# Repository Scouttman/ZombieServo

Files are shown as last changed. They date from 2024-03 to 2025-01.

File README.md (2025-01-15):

# ZombieServo
Motor Driver for some [aliexpress](https://www.aliexpress.com/item/1005004112490054.html) robotic serovos powered by simpleFOC and a STSPIN32g4
Runs simpleFOC forum post [here](https://community.simplefoc.com/t/zombie-servo-budget-high-torque-servo/4001)  
May also port the mit mini cheeta code to it if the torque control is good   
Position can be set with T i.e. set T6.28 will do one rotation (not sure why it is not a full rotation)  
The M command for simple foc is added but not tested  
20231021_143033 (1)
20231021_140654 (1)

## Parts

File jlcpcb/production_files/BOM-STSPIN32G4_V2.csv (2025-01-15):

Comment | Designator | Footprint | LCSC
Conn_01x03_MountingPin | J8 | JST_SH_BM03B-SRSS-TB_1x03-1MP_P1.00mm_Vertical | C145955
Conn_01x06_MountingPin | J9 | JST_SH_BM06B-SRSS-TB_1x06-1MP_P1.00mm_Vertical | C145958
20p | C18,C4 | C_0402_1005Metric | C1554
Q_Dual_NMOS_G1 | Q1,Q2,Q7 | V-DFN3030-8 (Type K) | C155503
33nf | C19 | C_0402_1005Metric | C1585
10uf 25v | C1,C6 | C_0805_2012Metric | C15850
USB_C_Receptacle_USB2.0 | J14 | USB_C_Receptacle_XKB_U262-16XN-4BVC11 | C165948
SS210 | D5 | D_SOD-323 | C191023
1N4148WS | D1,D10,D11,D12,D2,D7 | D_SOD-323 | C2128
LED | D3,D4_white2 | LED_0805_2012Metric | C2297
5.1k | R20 | R_0402_1005Metric | C23186
120 | R98 | R_0402_1005Metric | C25079
220 | R5,R6,R8 | R_0402_1005Metric | C25091
33 | R1,R13,R17,R18,R25,R4 | R_0402_1005Metric | C25105
10k | R11,R2,R3,R99 | R_0402_1005Metric | C25744
22k | R26,R27,R41,R47 | R_0402_1005Metric | C25768
1.5k | R23,R24,R44,R50 | R_0402_1005Metric | C25867
5.1k | R19 | R_0402_1005Metric | C25905
PRTR5V0U2X | D13 | SOT-143 | C2827688
1uF | C16,C24,C27 | C_0805_2012Metric | C28323
STSPIN32G4 | IC1 | STSPIN32G4 | C2858620
Conn_01x06_MountingPin | J6 | PinHeader_1x06_P1.27mm_Vertical | C2904934
Conn_01x12_MountingPin | J2 | 0.5K-A-12PBF | C2914207
BAT30k | D8 | D_SOD-523 | C2926449
100nF | C11,C41,C7,C9 | C_0402_1005Metric | C307331
18uh | L2 | L_1812_4532Metric | C394124
11k | R29,R53 | R_0402_1005Metric | C409665
1uF | C10,C8 | C_0402_1005Metric | C52923
220nF | C2 | C_0805_2012Metric | C5378
2.2uf | C21,C23,C26,C3 | C_1206_3216Metric | C650969
7mΩ | R15,R7 | R_1206_3216Metric | C76302
LED | D4_white1 | LED_0805_2012Metric | C84256
24mhz | Y3 | Crystal_SMD_3225-4Pin_3.2x2.5mm | C9002
TJA1057T/1Z | U2 | SOIC-8_3.9x4.9mm_P1.27mm | C961484
Conn_01x02_Female | J4 | PinHeader_1x02_P2.54mm_Vertical
Jumper_2_Bridged | JP8 | SolderJumper-2_P1.3mm_Bridged_RoundedPad1.0x1.5mm
NetTie_2 | NT1 | NetTie-2_SMD_Pad0.5mm
72.3k | R37 | R_0402_1005Metric
3.01k | R39 | R_0402_1005Metric
Jumper_2_Bridged | JP4 | SolderJumper-2_P1.3mm_Bridged_RoundedPad1.0x1.5mm
Jumper_2_Open | JP3 | SolderJumper-2_P1.3mm_Open_TrianglePad1.0x1.5mm
NetTie_2 | NT2 | NetTie-2_SMD_Pad0.5mm
MountingHole | H3 | MountingHole_2.2mm_M2
MountingHole | H2 | MountingHole_2.2mm_M2
MountingHole | H1 | MountingHole_2.2mm_M2
MountingHole | H4 | MountingHole_2.2mm_M2
Conn_01x03_Pin | J1 | JST_XH_B3B-XH-AM_1x03_P2.50mm_Vertical
Conn_01x03_MountingPin | J5 | JST_SH_BM03B-SRSS-TB_1x03-1MP_P1.00mm_Vertical
SW_Push | SW1 | SolderJumper-2_P1.3mm_Open_RoundedPad1.0x1.5mm
Jumper_2_Bridged | JP1 | SolderJumper-2_P1.3mm_Bridged_RoundedPad1.0x1.5mm

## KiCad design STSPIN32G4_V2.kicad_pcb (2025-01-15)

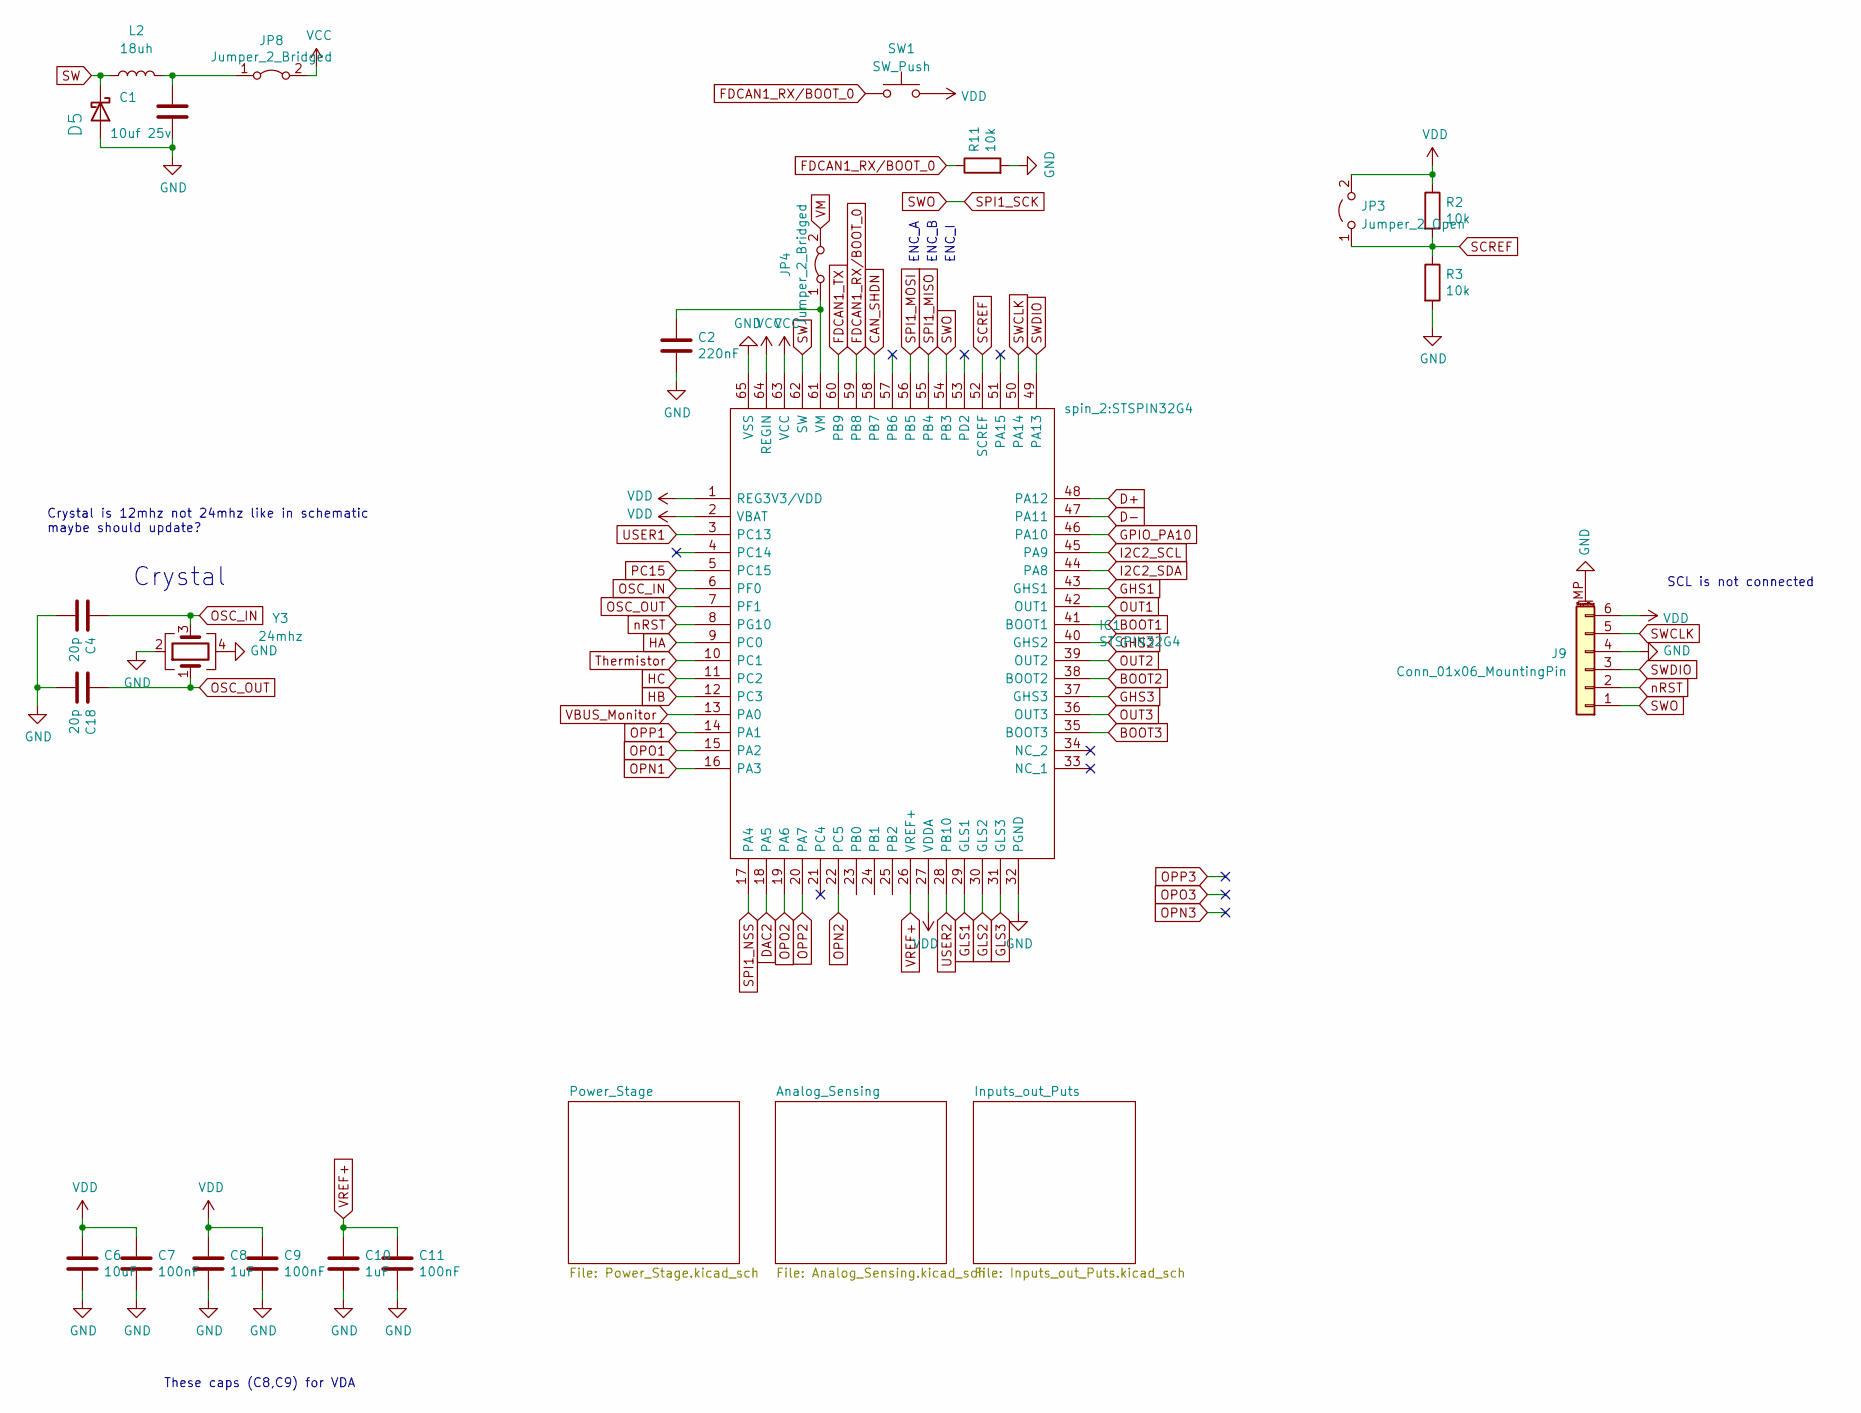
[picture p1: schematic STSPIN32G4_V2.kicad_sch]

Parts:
C1: 10uf 25v; C_0805_2012Metric
C2: 220nF; C_0805_2012Metric
C4, C18: 20p; C_0402_1005Metric
C6: 10uF; C_0805_2012Metric; LCSC Part C15850
C7, C9, C11: 100nF; C_0402_1005Metric
C8, C10: 1uF; C_0402_1005Metric
D5: SS210; D_SOD-323; LCSC C191023
IC1: STSPIN32G4; Manufacturer_Part_Number STSPIN32G4; Mouser Part Number 511-STSPIN32G4
J9: Conn_01x06_MountingPin; JST_SH_BM06B-SRSS-TB_1x06-1MP_P1.00mm_Vertical
JP3: Jumper_2_Open; SolderJumper-2_P1.3mm_Open_TrianglePad1.0x1.5mm
JP4, JP8: Jumper_2_Bridged; SolderJumper-2_P1.3mm_Bridged_RoundedPad1.0x1.5mm
L2: 18uh; L_1812_4532Metric; LCSC C394124
R2, R3, R11: 10k; R_0402_1005Metric
SW1: SW_Push; SolderJumper-2_P1.3mm_Open_RoundedPad1.0x1.5mm
Y3: 24mhz; Crystal_SMD_3225-4Pin_3.2x2.5mm; LCSC C9002

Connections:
BOOT1: IC1.41 (BOOT1); also elsewhere on the board
BOOT2: IC1.38 (BOOT2); also elsewhere on the board
BOOT3: IC1.35 (BOOT3); also elsewhere on the board
CAN_SHDN: IC1.58 (PB7); also elsewhere on the board
D+: IC1.48 (PA12); also elsewhere on the board
D-: IC1.47 (PA11); also elsewhere on the board
DAC2: IC1.18 (PA5)
FDCAN1_RX/BOOT_0: IC1.59 (PB8), R11.1, SW1.1; also elsewhere on the board
FDCAN1_TX: IC1.60 (PB9); also elsewhere on the board
GHS1: IC1.43 (GHS1); also elsewhere on the board
GHS2: IC1.40 (GHS2); also elsewhere on the board
GHS3: IC1.37 (GHS3); also elsewhere on the board
GLS1: IC1.29 (GLS1); also elsewhere on the board
GLS2: IC1.30 (GLS2); also elsewhere on the board
GLS3: IC1.31 (GLS3); also elsewhere on the board
GND: C1.2, C2.2, C4.2, C6.2, C7.2, C8.2, C9.2, C10.2, C11.2, C18.2, D5.2 (A), IC1.32 (PGND), IC1.65 (VSS), J9.4, J9.MP (MountPin), R3.2, R11.2, Y3.2, Y3.4; also elsewhere on the board
GPIO_PA10: IC1.46 (PA10); also elsewhere on the board
HA: IC1.9 (PC0); also elsewhere on the board
HB: IC1.12 (PC3); also elsewhere on the board
HC: IC1.11 (PC2); also elsewhere on the board
I2C2_SCL: IC1.45 (PA9); also elsewhere on the board
I2C2_SDA: IC1.44 (PA8); also elsewhere on the board
unnamed: C1.1, JP8.1 (A), L2.2
OPN1: IC1.16 (PA3); also elsewhere on the board
OPN2: IC1.22 (PC5); also elsewhere on the board
OPO1: IC1.15 (PA2); also elsewhere on the board
OPO2: IC1.19 (PA6); also elsewhere on the board
OPP1: IC1.14 (PA1); also elsewhere on the board
OPP2: IC1.20 (PA7); also elsewhere on the board
OSC_IN: C4.1, IC1.6 (PF0), Y3.3
OSC_OUT: C18.1, IC1.7 (PF1), Y3.1
OUT1: IC1.42 (OUT1); also elsewhere on the board
OUT2: IC1.39 (OUT2); also elsewhere on the board
OUT3: IC1.36 (OUT3); also elsewhere on the board
PC15: IC1.5 (PC15)
SCREF: IC1.52 (SCREF), JP3.1 (A), R2.2, R3.1
SPI1_MISO: IC1.55 (PB4); also elsewhere on the board
SPI1_MOSI: IC1.56 (PB5); also elsewhere on the board
SPI1_NSS: IC1.17 (PA4); also elsewhere on the board
SPI1_SCK: IC1.54 (PB3), J9.1; also elsewhere on the board
SW: D5.1 (K), IC1.62 (SW), L2.1
SWCLK: IC1.50 (PA14), J9.5
SWDIO: IC1.49 (PA13), J9.3
Thermistor: IC1.10 (PC1); also elsewhere on the board
USER1: IC1.3 (PC13); also elsewhere on the board
USER2: IC1.28 (PB10); also elsewhere on the board
VBUS_Monitor: IC1.13 (PA0); also elsewhere on the board
VCC: IC1.63 (VCC), IC1.64 (REGIN), JP8.2 (B)
VDD: C6.1, C7.1, C8.1, C9.1, IC1.1 (REG3V3/VDD), IC1.2 (VBAT), IC1.27 (VDDA), J9.6, JP3.2 (B), R2.1, SW1.2; also elsewhere on the board
VREF+: C10.1, C11.1, IC1.26 (VREF+); also elsewhere on the board
nRST: IC1.8 (PG10), J9.2

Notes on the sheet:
ENC_I
These caps (C8,C9) for VDA
ENC_B
Crystal
ENC_A
Crystal is 12mhz not 24mhz like in schematic maybe should update?
SCL is not connected

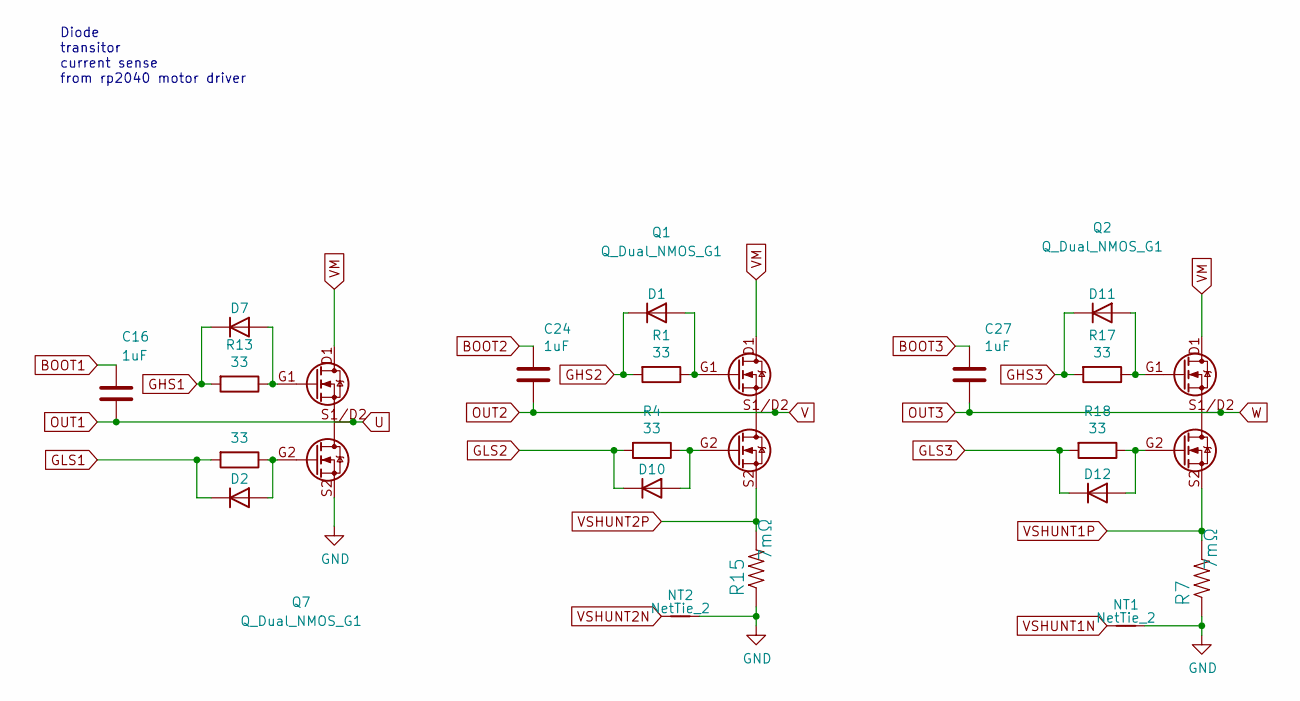
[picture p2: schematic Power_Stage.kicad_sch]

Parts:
C16, C24, C27: 1uF; C_0805_2012Metric; LCSC Part C28323
D1, D2, D7, D10, D11, D12: 1N4148WS; D_SOD-323; LCSC C2128
NT1, NT2: NetTie_2; NetTie-2_SMD_Pad0.5mm
Q1, Q2, Q7: Q_Dual_NMOS_G1; V-DFN3030-8 (Type K)
R1, R4, R13, R17, R18, R25: 33; R_0402_1005Metric
R7, R15: 7mΩ; R_1206_3216Metric; LCSC C76302

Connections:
BOOT1: C16.2; also elsewhere on the board
BOOT2: C24.2; also elsewhere on the board
BOOT3: C27.2; also elsewhere on the board
GHS1: D7.1 (K), R13.2; also elsewhere on the board
GHS2: D1.1 (K), R1.2; also elsewhere on the board
GHS3: D11.1 (K), R17.2; also elsewhere on the board
GLS1: D2.1 (K), R25.2; also elsewhere on the board
GLS2: D10.1 (K), R4.2; also elsewhere on the board
GLS3: D12.1 (K), R18.2; also elsewhere on the board
GND: NT1.2, NT2.2, Q7.S2, R7.1, R15.1; also elsewhere on the board
unnamed: D1.2 (A), Q1.G1, R1.1
unnamed: D2.2 (A), Q7.G2, R25.1
unnamed: D7.2 (A), Q7.G1, R13.1
unnamed: D10.2 (A), Q1.G2, R4.1
unnamed: D11.2 (A), Q2.G1, R17.1
unnamed: D12.2 (A), Q2.G2, R18.1
OUT1: C16.1, Q7.S1/D2; also elsewhere on the board
OUT2: C24.1, Q1.S1/D2; also elsewhere on the board
OUT3: C27.1, Q2.S1/D2; also elsewhere on the board
VSHUNT1N: NT1.1; also elsewhere on the board
VSHUNT1P: Q2.S2, R7.2; also elsewhere on the board
VSHUNT2N: NT2.1; also elsewhere on the board
VSHUNT2P: Q1.S2, R15.2; also elsewhere on the board

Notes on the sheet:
Diode transitor current sense from rp2040 motor driver

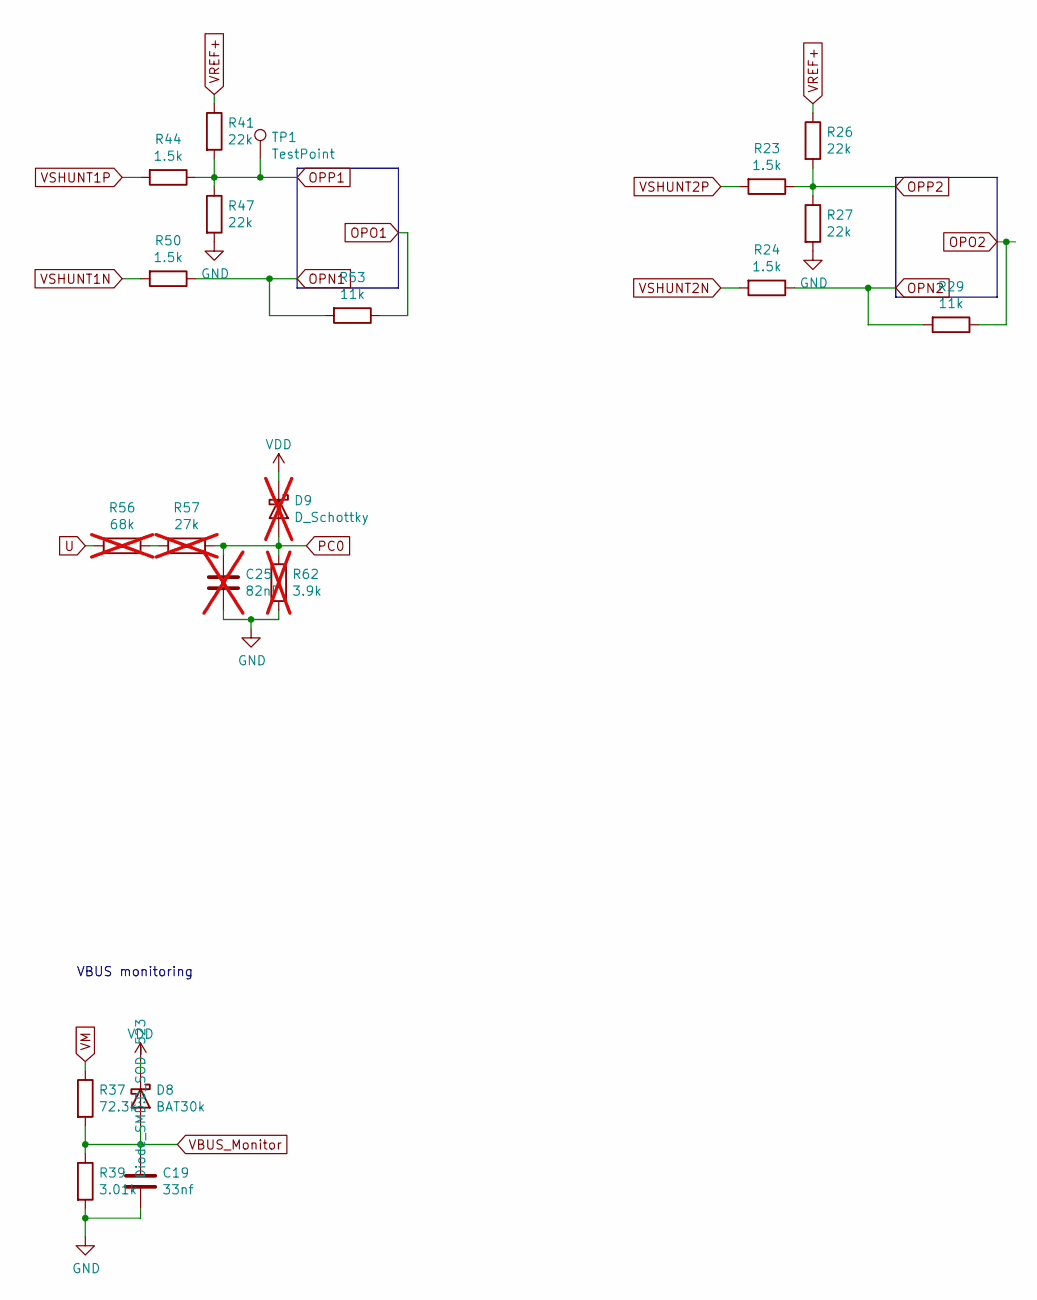
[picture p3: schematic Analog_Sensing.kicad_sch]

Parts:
C19: 33nf; C_0402_1005Metric
C25: 82nF; C_0402_1005Metric; not fitted
D8: BAT30k; D_SOD-523
D9: D_Schottky; D_SOD-523; not fitted
R23, R24, R44, R50: 1.5k; R_0402_1005Metric
R26, R27, R41, R47: 22k; R_0402_1005Metric
R29, R53: 11k; R_0402_1005Metric; LCSC C409665
R37: 72.3k; R_0402_1005Metric
R39: 3.01k; R_0402_1005Metric
R56: 68k; R_0402_1005Metric; not fitted
R57: 27k; R_0402_1005Metric; not fitted
R62: 3.9k; R_0402_1005Metric; not fitted
TP1: TestPoint; TestPoint_Pad_D2.0mm

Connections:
GND: C19.2, C25.2, R27.2, R39.2, R47.2, R62.2; also elsewhere on the board
unnamed: C25.1, D9.2 (A), R57.1, R62.1
unnamed: R56.1, R57.2
OPN1: R50.1, R53.2; also elsewhere on the board
OPN2: R24.1, R29.2; also elsewhere on the board
OPO1: R53.1; also elsewhere on the board
OPO2: R29.1; also elsewhere on the board
OPP1: R41.2, R44.1, R47.1, TP1.1; also elsewhere on the board
OPP2: R23.1, R26.2, R27.1; also elsewhere on the board
VBUS_Monitor: C19.1, D8.2 (A), R37.2, R39.1; also elsewhere on the board
VDD: D8.1 (K), D9.1 (K); also elsewhere on the board
VREF+: R26.1, R41.1; also elsewhere on the board
VSHUNT1N: R50.2; also elsewhere on the board
VSHUNT1P: R44.2; also elsewhere on the board
VSHUNT2N: R24.2; also elsewhere on the board
VSHUNT2P: R23.2; also elsewhere on the board

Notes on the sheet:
VBUS monitoring

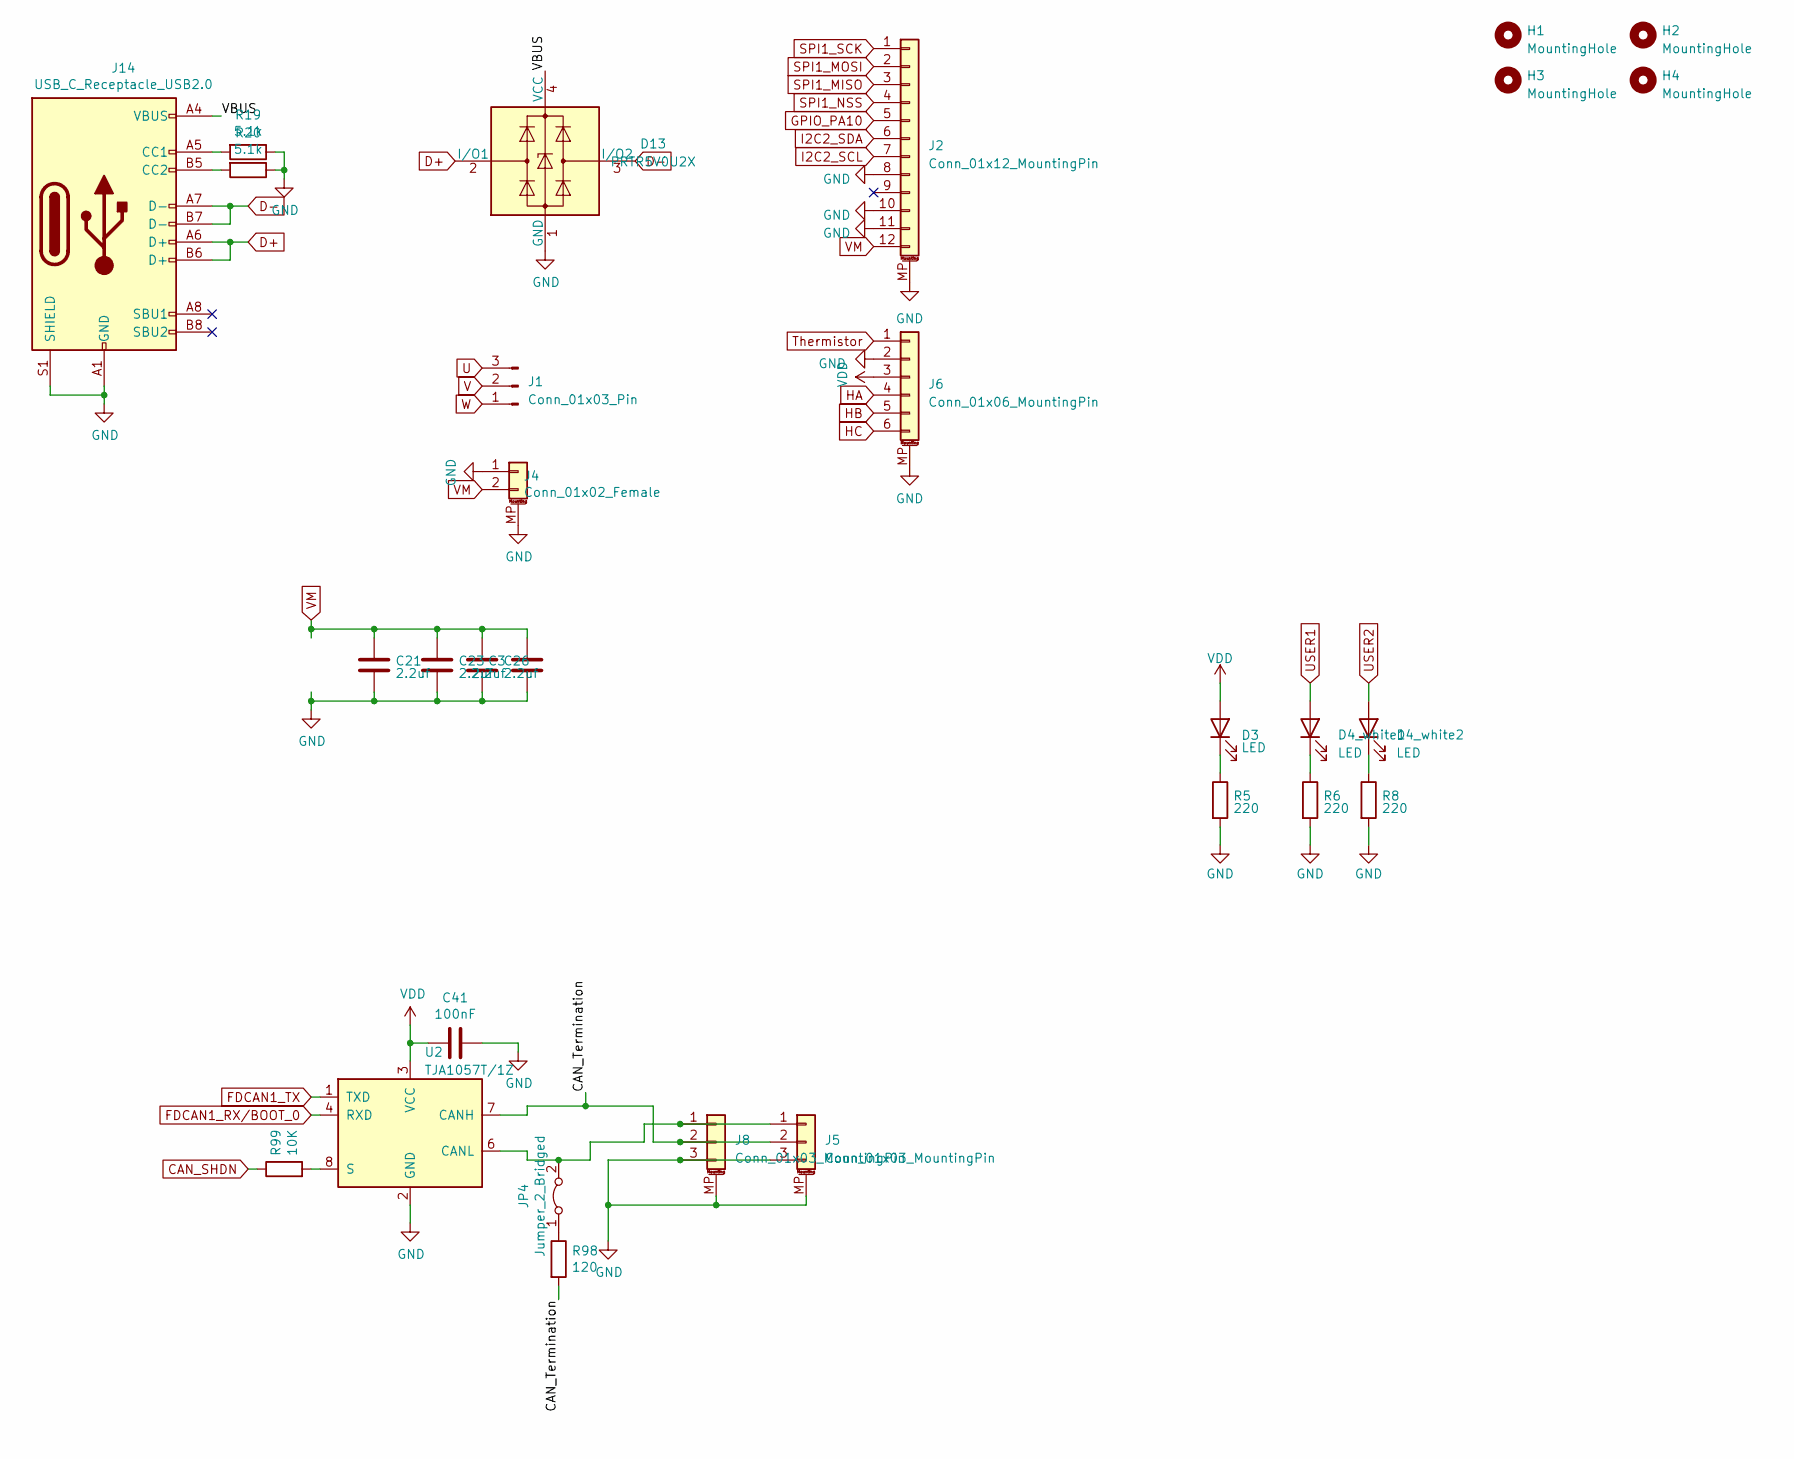
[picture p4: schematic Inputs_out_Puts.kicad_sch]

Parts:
C3, C21, C23, C26: 2.2uf; C_1206_3216Metric; LCSC Part C650969
C41: 100nF; C_0402_1005Metric
D3, D4_white1, D4_white2: LED; LED_0805_2012Metric
D13: PRTR5V0U2X; SOT-143
H1, H2, H3, H4: MountingHole; MountingHole_2.2mm_M2
J1: Conn_01x03_Pin; JST_XH_B3B-XH-AM_1x03_P2.50mm_Vertical
J2: Conn_01x12_MountingPin; 0.5K-A-12PBF; LCSC C2914207
J4: Conn_01x02_Female; PinHeader_1x02_P2.54mm_Vertical
J5, J8: Conn_01x03_MountingPin; JST_SH_BM03B-SRSS-TB_1x03-1MP_P1.00mm_Vertical
J6: Conn_01x06_MountingPin; PinHeader_1x06_P1.27mm_Vertical; LCSC C2904934
J14: USB_C_Receptacle_USB2.0; USB_C_Receptacle_XKB_U262-16XN-4BVC11; LCSC Part C165948
JP4: Jumper_2_Bridged; SolderJumper-2_P1.3mm_Bridged_RoundedPad1.0x1.5mm
R5, R6, R8: 220; R_0402_1005Metric
R19: 5.1k; R_0402_1005Metric
R20: 5.1k; R_0402_1005Metric; LCSC Part C23186
R98: 120; R_0402_1005Metric
R99: 10K; R_0402_1005Metric
U2: TJA1057T/1Z; SOIC-8_3.9x4.9mm_P1.27mm; LCSC C961484

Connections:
/Inputs_out_Puts/CAN_Termination: J5.2, J8.2, R98.2, U2.7 (CANH)
/Inputs_out_Puts/VBUS: D13.4 (VCC), J14.A4 (VBUS), J14.A9 (VBUS), J14.B4 (VBUS), J14.B9 (VBUS)
CAN_SHDN: R99.1; also elsewhere on the board
D+: D13.2 (I/O1), J14.A6 (D+), J14.B6 (D+); also elsewhere on the board
D-: D13.3 (I/O2), J14.A7 (D-), J14.B7 (D-); also elsewhere on the board
FDCAN1_RX/BOOT_0: U2.4 (RXD); also elsewhere on the board
FDCAN1_TX: U2.1 (TXD); also elsewhere on the board
GND: C3.2, C21.2, C23.2, C26.2, C41.1, D13.1 (GND), J2.8, J2.10, J2.11, J2.MP (MountPin), J4.1, J4.MP (MountPin), J5.3, J5.MP (MountPin), J6.2, J6.MP (MountPin), J8.3, J8.MP (MountPin), J14.A1 (GND), J14.A12 (GND), J14.B1 (GND), J14.B12 (GND), J14.S1 (SHIELD), R5.2, R6.2, R8.2, R19.1, R20.1, U2.2 (GND); also elsewhere on the board
GPIO_PA10: J2.5; also elsewhere on the board
HA: J6.4; also elsewhere on the board
HB: J6.5; also elsewhere on the board
HC: J6.6; also elsewhere on the board
I2C2_SCL: J2.7; also elsewhere on the board
I2C2_SDA: J2.6; also elsewhere on the board
unnamed: D3.1 (K), R5.1
unnamed: D4_white1.1 (K), R6.1
unnamed: D4_white2.1 (K), R8.1
unnamed: J14.A5 (CC1), R19.2
unnamed: J14.B5 (CC2), R20.2
unnamed: R99.2, U2.8 (S)
OUT1: J1.3; also elsewhere on the board
OUT2: J1.2; also elsewhere on the board
OUT3: J1.1; also elsewhere on the board
SPI1_MISO: J2.3; also elsewhere on the board
SPI1_MOSI: J2.2; also elsewhere on the board
SPI1_NSS: J2.4; also elsewhere on the board
SPI1_SCK: J2.1; also elsewhere on the board
Thermistor: J6.1; also elsewhere on the board
USER1: D4_white1.2 (A); also elsewhere on the board
USER2: D4_white2.2 (A); also elsewhere on the board
VDD: C41.2, D3.2 (A), J6.3, U2.3 (VCC); also elsewhere on the board

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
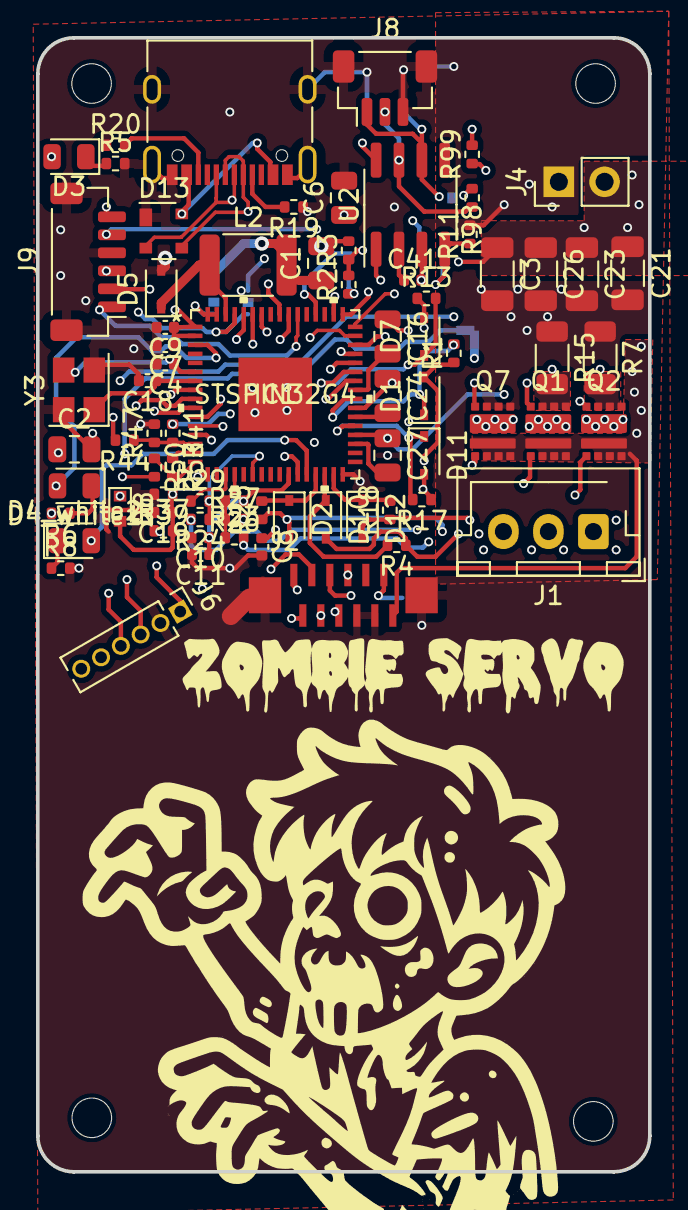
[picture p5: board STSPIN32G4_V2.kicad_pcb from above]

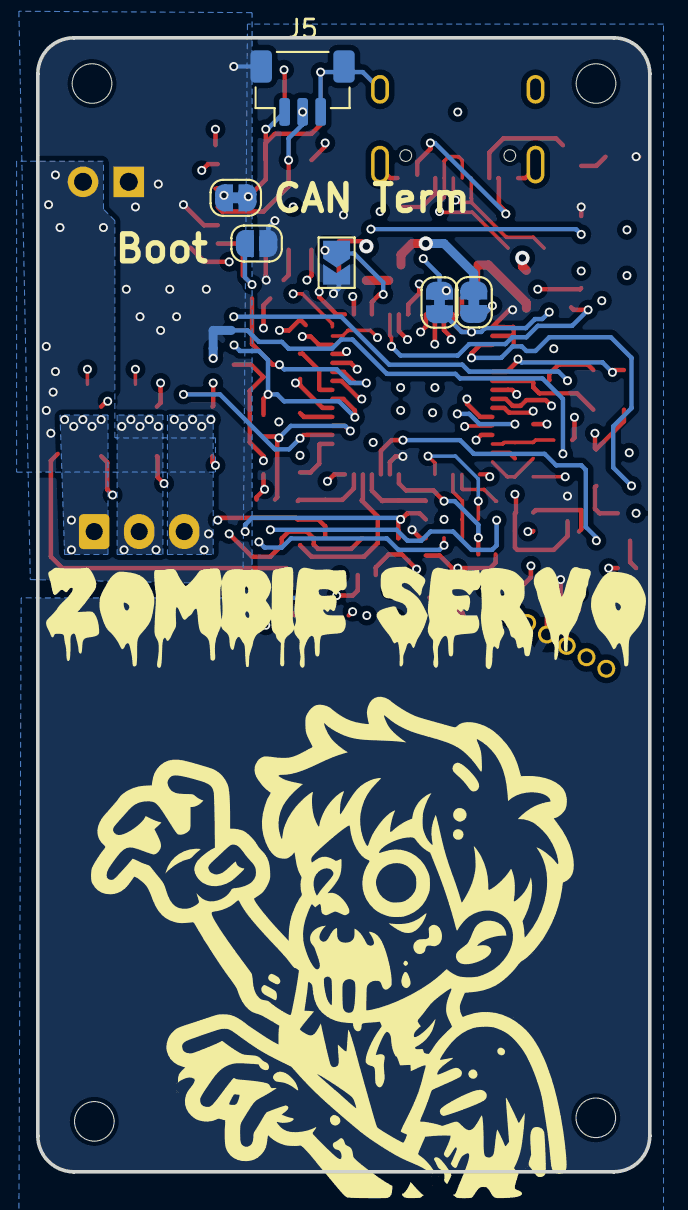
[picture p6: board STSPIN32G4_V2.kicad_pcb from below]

Board: 4 copper layers, 34.0 x 63.0 mm, 87 parts (8 on the bottom side), 71 nets.

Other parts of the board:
JP1: Jumper_2_Bridged; SolderJumper-2_P1.3mm_Bridged_RoundedPad1.0x1.5mm

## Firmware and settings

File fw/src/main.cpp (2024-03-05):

#include <Arduino.h>
#include <SimpleFOC.h>
#include "drivers/stspin32g4/STSPIN32G4.h"
// #include "encoders/ma730/MA730.h"
#include "encoders/ma730/MagneticSensorMA730.h"

#define LED_WHITE PB_10 
#define LED_RED PC_13
#define MAG_CS PA4
#define MOIS_PIN PB5
#define MISO_PIN PB4
#define SCLK_PIN PB3
#define SSI_SSCK_FREQUENCY  10000       //SSI SSCK Clock frequency in Hz #TODO increase back to 100k

STSPIN32G4 driver = STSPIN32G4();
BLDCMotor motor = BLDCMotor(1); // for drive module
HallSensor sensor = HallSensor(PC0, PC2, PC3, 1);
MagneticSensorMA730 output_encoder = MagneticSensorMA730(MAG_CS);
// interrupt routine intialisation
void doA(){sensor.handleA();}
void doB(){sensor.handleB();}
void doC(){sensor.handleC();}

// External digital encoder
SPIClass SPI_1(MOIS_PIN, MISO_PIN, SCLK_PIN);
PIDController PID_ang{1000.0,0.0,0.0,0,5000}; // PID controller for the output angle

// angle set point variable
float target_angle = 0;
Commander command = Commander(Serial);
void doTarget(char* cmd) { command.scalar(&target_angle, cmd); }
void doMotor(char* cmd) { command.motor(&motor, cmd); }

int counter = 0;

void setup() {
  Serial.begin();
  Serial.println("Start");
  command.add('M',doMotor,"motor");
  // add target command T
  command.add('T', doTarget, "target angle");

  // setup timer 6 to count micro seconds as the micro second timer inside stduino is slow
  __HAL_RCC_TIM6_CLK_ENABLE();
  TIM6->PSC = HAL_RCC_GetPCLK1Freq()/1000000 - 1;
  TIM6->CR1 = TIM_CR1_CEN;

  /* Initialize all configured peripherals */
  pinMode(LED_WHITE, OUTPUT);
  pinMode(LED_RED, OUTPUT);
  
  // initialise encoder hardware
  sensor.init();
  sensor.enableInterrupts(doA, doB, doC);
  motor.linkSensor(&sensor);
  output_encoder.init(&SPI_1);

  // driver
  driver.voltage_power_supply = 17.0f;
  driver.voltage_limit = 17.0f;
  driver.init();
  motor.voltage_limit = driver.voltage_limit / 2.0f;
  motor.controller = MotionControlType::velocity;
  // set the torque control type
  motor.phase_resistance = 12.5; // 12.5 Ohms
  // set motion control loop to be used
  // motor.controller = MotionControlType::torque;
  motor.linkDriver(&driver);
  motor.init();

  motor.PID_velocity.P = 0.001f;
  motor.PID_velocity.I = 0.0f;
  motor.PID_velocity.D = 0;

  // initialize motor
  motor.init();
  // align encoder and start FOC
  motor.initFOC();
  // driver.voltage_limit = 6;

  Serial.println(F("Motor ready."));
  Serial.println(F("Set the target angle using serial terminal:"));
}

void loop() {
    // main FOC algorithm function
  motor.loopFOC();
  
  float vel_set = PID_ang(output_encoder.getAngle()-target_angle);
  motor.move(vel_set);
  if(driver.isFault()){
    digitalWrite(LED_WHITE, HIGH);
    digitalWrite(LED_RED, HIGH);
  }else{
    digitalWrite(LED_WHITE, LOW);
    digitalWrite(LED_RED, LOW);
  }
  // real-time monitoring calls
  motor.monitor();
  // real-time commander calls
  command.run();
  if(counter++%10000 == 0){
    Serial.print("Ang:");
    Serial.println(output_encoder.getAngle()); 

  }
  output_encoder.update();
}

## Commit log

2024-02-24 fw for board
2024-03-05 added the external angle sensor
2025-01-15 attempt at cleaning up
    [Analog_Sensing.kicad_sch, BOM-STSPIN32G4.csv, BOM-STSPIN32G4_V2.csv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]

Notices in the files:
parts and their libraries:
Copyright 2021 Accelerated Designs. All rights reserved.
